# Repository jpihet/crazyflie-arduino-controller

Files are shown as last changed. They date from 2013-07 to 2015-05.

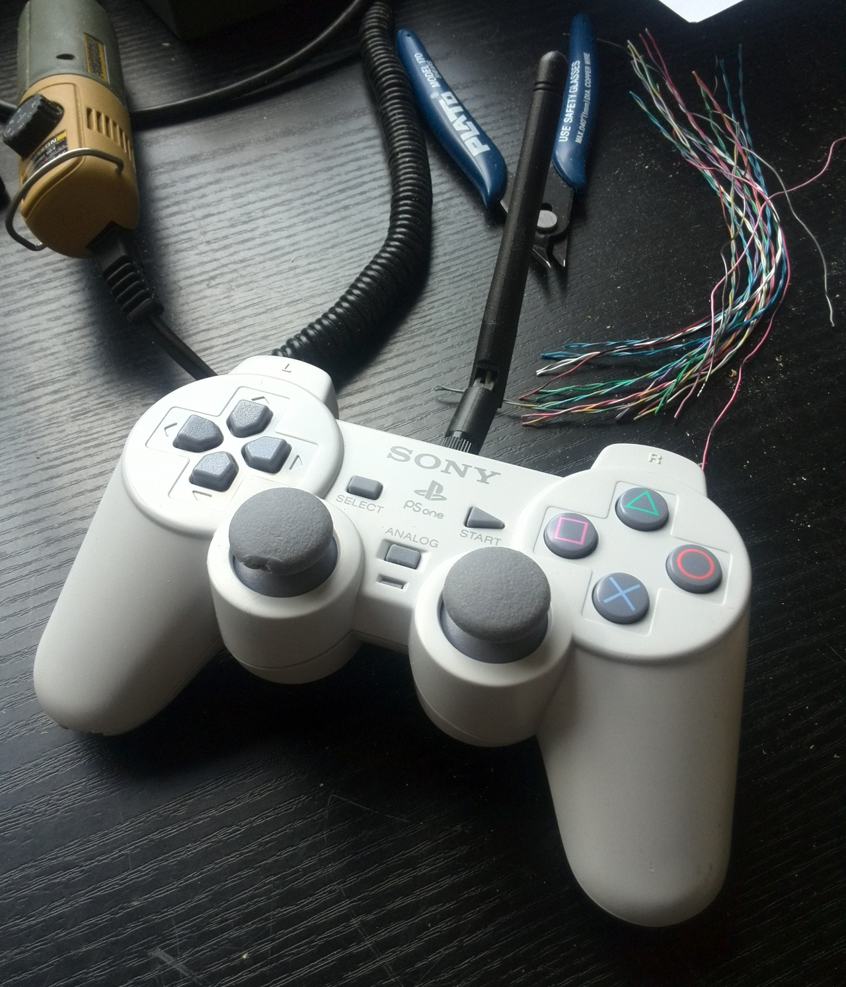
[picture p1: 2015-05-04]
Build_info/Crazyflie-Arduino-PS1_2.jpg

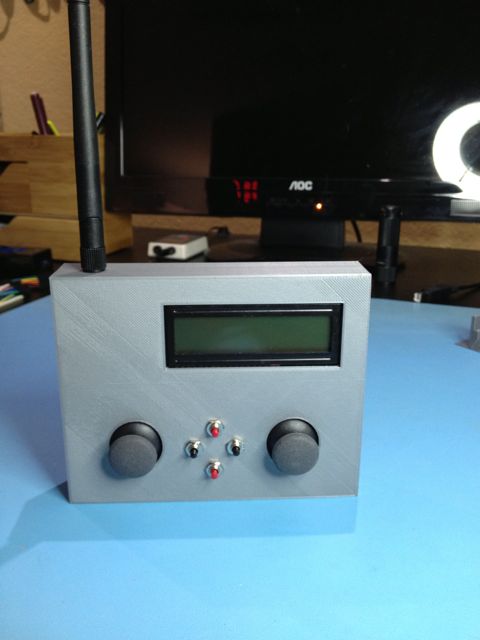
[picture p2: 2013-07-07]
Build_info/Case Front.jpg

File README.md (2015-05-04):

Crazyflie Arduino Controller Demo

This is a simple Arduino sketch to demonstrate the capability to use an Arduino
Nano connected to a h(ij)acked PS1 controller and a nRF24L01+PA board to fly a
CrazyFlie 2.0.

From tbitson's original project and code.

Wiring:
See code listing

Photos: see Build Info

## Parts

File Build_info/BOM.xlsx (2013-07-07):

Name | Source | PN | ID | Qty | Cost Ea | Comment
nRF24L001+ Breakout Board | Sparkfun | WRL-00705 |  | 1 | 19.95
Joystick, Thumb | Sparkfun | COM-09032 | JS1, JS2 | 2 | 3.95
Joystick Breakout Board | Sparkfun | BOB-09110 |  | 2 | 1.95
Arduino Pro Mini 5v 16MHz | Sparkfun | DEV-11113 | Arduino | 1 | 9.95
Serial LCD | Adafruit | 782 | LCD | 1 | 24.95
Antenna, 2.4 GHz Dipole | Adafruit | 944 | ANT1 | 1 | 6.95
Antenna, 2.4 GHz Dipole 5dBi Gain | Adafruit | 945 |  |  | 8.95 | Longer Range Option
Male Headers, strip | Adafruit | 392 |  | 100 | 7.95 | 10 Strips of 36
Jumpers, Female to Female | Sparkfun | PRT-08430 |  | 3 | 3.95 | pack of 10
Battery, Li Ion | Adafruit | 258 | B1 | 1 | 22.95 | Alternate - Use 3 AA
Charger/Booster, LiPo | Sparkfun | PRT-11231 |  | 1 | 19.95 | Convert battery to 5V
Switch, SPST | various | S7 |  | 1
Switch, pushbutton N.O. | various |  |  | 4
Proto-board for Power Bus | Adafruit | 589 |  | 1 | 8.95 | Pack of 3, only need 1
Case, 3-D Printed

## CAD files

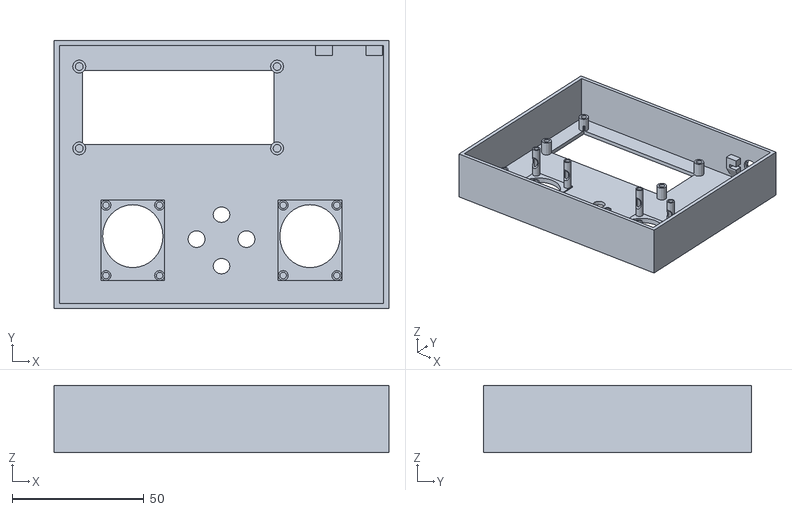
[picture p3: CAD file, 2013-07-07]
Build_info/crazyflie_controller_case.stl
127.0 x 101.6 x 25.4

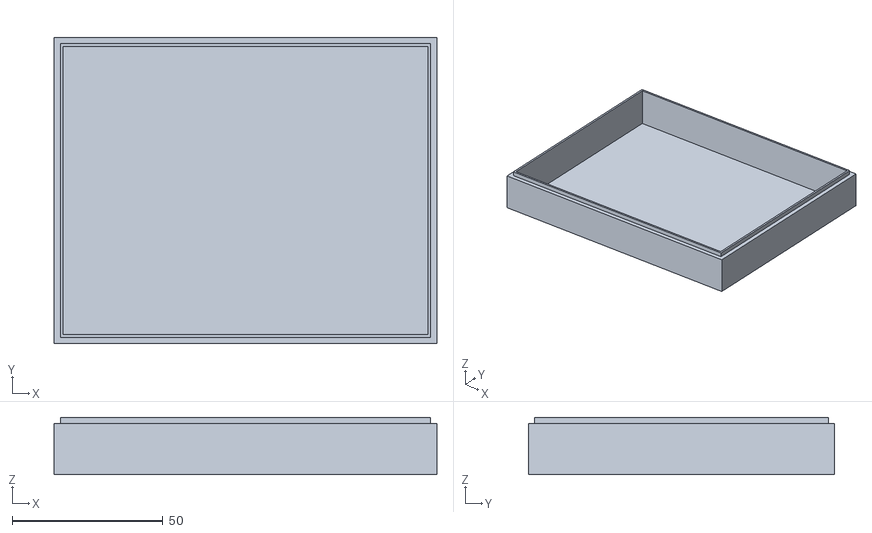
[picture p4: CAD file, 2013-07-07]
Build_info/crazyflie_controller_case_back.stl
127.0 x 101.6 x 19.1

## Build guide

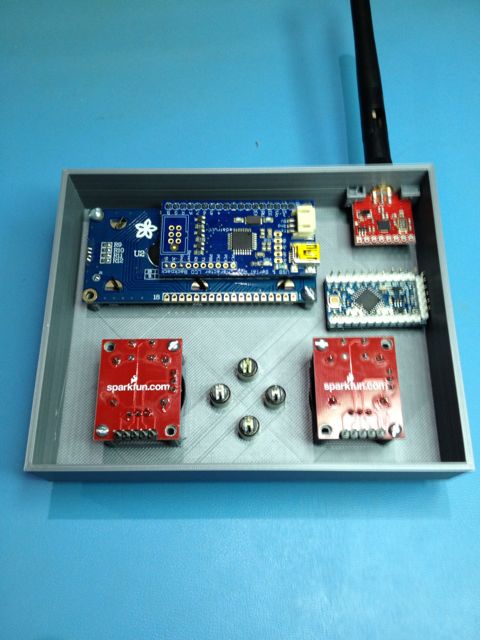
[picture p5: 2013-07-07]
Build_info/Inside - prior to wiring.jpg

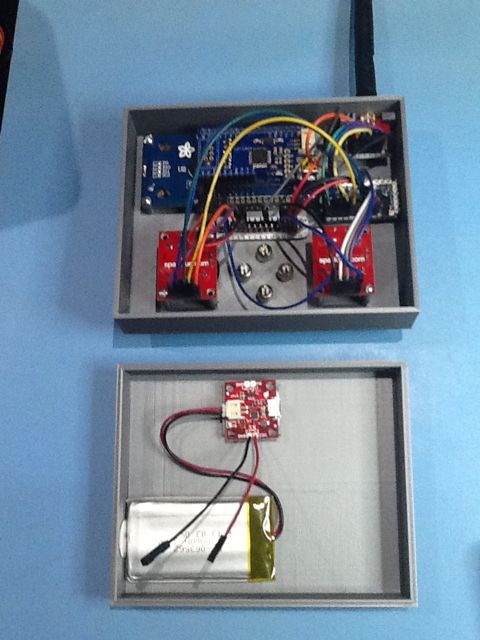
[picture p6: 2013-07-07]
Build_info/Inside - after wiring.jpg

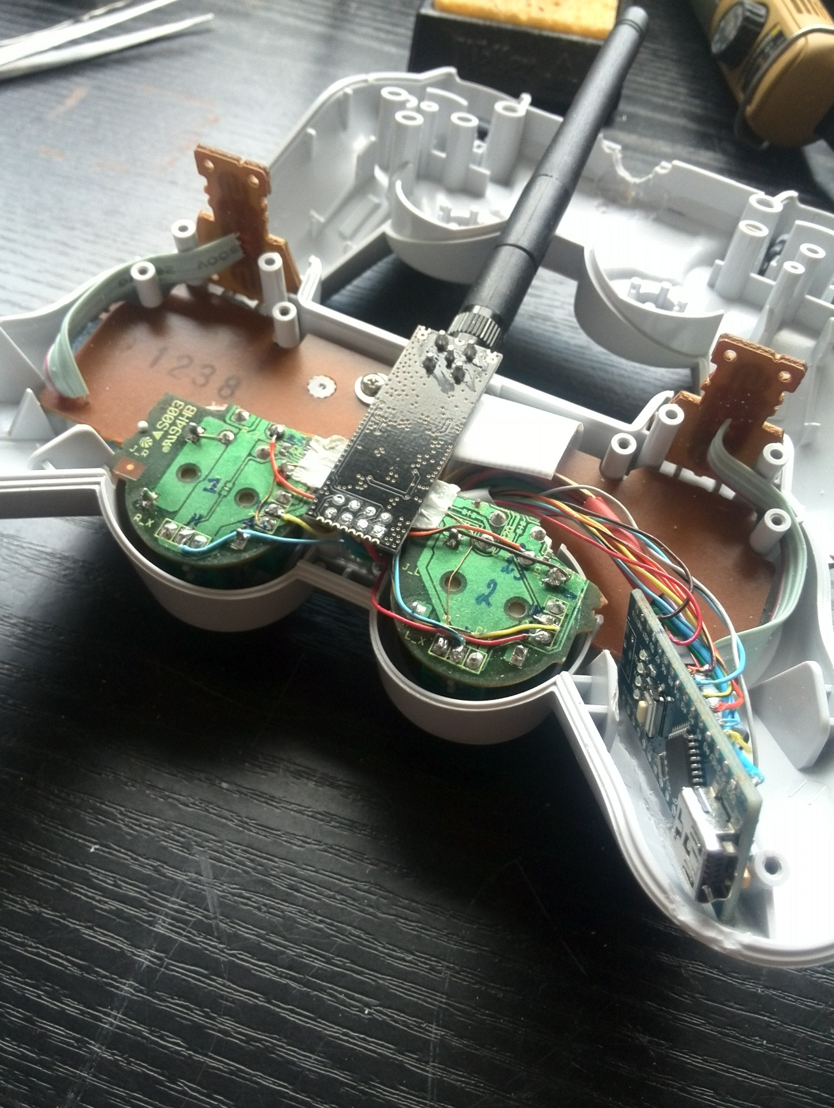
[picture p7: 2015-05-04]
Build_info/Crazyflie-Arduino-PS1_1.jpg

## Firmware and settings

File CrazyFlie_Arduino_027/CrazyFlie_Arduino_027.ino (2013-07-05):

/*   CrazyFlie Controller
 *   version 0.27  7/04/13 tbitson
 *
 * This program demonstarts controlling a CrazyFlie Quadcopter
 * using an Arduino. Based on the RF24 library by maniacbug at
 * https://github.com/maniacbug
 *
 * this is a very early prototype just to show its possible
 *
 *     TODO: 
 *     Get ACK packet to work
 *     Use 4 pushbuttons to adjust trim
 *     Add Logging & display remote battery capacity on LCD
 *     Fix thrust smoothing
 *     Convert LCD routines to a Arduinbo Libray
 *     Eliminate the RF24 library with direct nRF24L01 comm
 */


#include <SPI.h>
#include "nRF24L01.h"
#include "RF24.h"
#include "printf.h"
#include <SoftwareSerial.h>


// my defines
#define ulong uint32_t
#define uint  uint16_t

// enable debug prints by setting to 1
const boolean DEBUG = 0;

// connections
#define JS1_V   A0    // Thrust
#define JS1_H   A1    // Yaw
#define JS1_S   A2    // TBD

#define JS2_V   A3    // Pitch
#define JS2_H   A4    // Yaw
#define JS2_S   A5    // TBD

#define LCD_RX  2    // Rx
#define LCD_TX  3    // not connected

#define RF24_MOSI  11
#define RF24_MISO  12
#define RF24_SCK   13
#define RF24_IRQ   8   // not connected
#define RF24_CE    9
#define RF24_CSN   10

#define SW1    4    // switches unused in this version
#define SW2    5
#define SW3    6
#define SW4    7

#define LED  8

// from crazyflie firmware commander.c 
#define MIN_THRUST  10000
#define MAX_THRUST  50000
#define MIN_PITCH -30.0
#define MAX_PITCH  30.0
#define MIN_ROLL  -30.0
#define MAX_ROLL   30.0
#define MIN_YAW   -200.0
#define MAX_YAW    200.0

// hard coded offset values TODO: use switches to adjust
const int JS1_V_OFFSET = 497;    // thrust
const int JS1_H_OFFSET = 508;    // yaw
const int JS2_V_OFFSET = 510;    // pitch
const int JS2_H_OFFSET = 514;    // roll

// program defines
#define LOOP_TIME    100  // 100ms = 10 updates per second
#define SLEEP_MODE   0
#define PWR_ON_MODE  1

// joystick full scale value. Range 0 +/- 512 counts
const float JS_RANGE = 512.0;

// user set trim values TODO: store in EEPROM
int pitchOffset = 0;
int rollOffset = 0;
int yawOffset = 0;

// experimental thrust smoothing levels
const float ALPHA_UP = .50;
const float ALPHA_DOWN = .80;
float smoothedThrust = 0.0;


// Init RF24 lib. Pass CE and CSN pins
RF24 radio(RF24_CE, RF24_CSN);

// init LCD Serial port. Pass Rx and Tx pins
SoftwareSerial lcd(2, 3);


// define the packet we want to send
typedef struct
{
  byte addr;
  float roll;
  float pitch;
  float yaw;
  uint  thrust;
} 
cmdPacket;

// create an instance of the packet
cmdPacket crtp; 

// TODO: create a union with cmpPacket and byte array 

// send & receive array. Lame way to send struct
char payload[15];

// define a struct to store current state of I/O
typedef struct
{
  int thrust;
  int pitch;
  int yaw;
  int roll;
  boolean sw1;
  boolean sw2;
}  
controls;

//make an instance of the controls struct
controls cntr;


// program vars
ulong lastLoopTime = 0;
byte  mode = PWR_ON_MODE;





void setup(void)
{
  // let everything powerup & init
  delay(2000);

  Serial.begin(57600);
  Serial.println("CrazyFlie Arduino Controller ver 0.25");
  printf_begin();

  lcd.begin(57600);
  initSerialLCD();
  setLCDColor(0xFF, 0xFF, 0xFF);  // white
  lcd.print("CrazyFlie v0.25");

  // set up pin modes
  pinMode(LED, OUTPUT);
  pinMode(JS1_S, INPUT);
  pinMode(JS2_S, INPUT);

  // enable internal pullups on joystick switches
  digitalWrite(JS1_S, HIGH);
  digitalWrite(JS2_S, HIGH);

  // TODO: read control offsets if JS button is pushed
  // and store in EEPROM


  // define initial values for packet
  crtp.addr   = 0x30;
  crtp.roll   = 0.0;
  crtp.pitch  = 0.0;
  crtp.yaw    = 0.0;
  crtp.thrust = 0;

  // Setup and configure rf radio
  radio.begin();

  // enable dynamic payloads, ch 10, data rate 250K
  radio.enableDynamicPayloads();
  radio.setChannel(10);
  radio.setDataRate(RF24_250KBPS);
  radio.setRetries(5,3);
  radio.setCRCLength(RF24_CRC_16);
  radio.openWritingPipe(0xE7E7E7E7E7LL);
  radio.openReadingPipe(1, 0xE7E7E7E7E7LL);
  delay(100);

  // Dump the configuration of the rf unit for debugging
  if (DEBUG) radio.printDetails();

  // Start listening
  radio.startListening();

  Serial.println("setup done");
  //clearLCD();
}




void loop(void)
{
  // loop if desired time has passed
  if ((millis() - lastLoopTime) > LOOP_TIME)
  {
    lastLoopTime = millis();

    // read controls
    readControls();

    // check if we should enter/exit low power mode
    checkPowerStatus();

    // if low power mode, just exit
    if (mode == SLEEP_MODE) return;

    // scale controls to expected CF values
    processControls();

    if (DEBUG) printCntrValues();
    if (DEBUG) printCRTPValues();

    // send data to Cazyflie
    sendData();

    // check various stuff
    checkStatus();

    // show current status and info on LCD
    updateLCD();
  }
}





void readControls()
{
  // read pitch and roll on joystick 1
  cntr.thrust = analogRead(JS1_V);
  cntr.yaw    = analogRead(JS1_H);
  cntr.sw1    = !digitalRead(JS1_S);

  // read throttle & yaw on joystick 2
  cntr.pitch = analogRead(JS2_V);
  cntr.roll  = analogRead(JS2_H);
  cntr.sw2   = !digitalRead(JS2_S);

  // TODO: add debouce to switches if pressed
}


void processControls()
{
  // thrust is 10000 to 50000
  // pitch is -30.00 to +30.00
  // roll is -3000 to +30.00
  // yaw is -199.99 to +199.99

  float alpha;

  // first subtract offsets from joystick
  cntr.thrust -= JS1_V_OFFSET;
  cntr.yaw -= JS1_H_OFFSET;
  cntr.pitch -= JS2_V_OFFSET;
  cntr.roll -= JS2_H_OFFSET;

  // scale to crazyflie values
  float thrust = ((float)cntr.thrust - 10.0) * MAX_THRUST/512.0;
  crtp.pitch = (float)cntr.pitch * MAX_PITCH/512.0 * -1.0;
  crtp.roll =  (float)cntr.roll * MAX_ROLL/512.0 * -1.0;
  crtp.yaw =   (float)cntr.yaw * MAX_YAW/512.0;

  // experimental filter to smooth thrust power
  if (thrust < 0) thrust = 0;
  if (thrust < smoothedThrust)
    alpha = ALPHA_DOWN;
  else
    alpha = ALPHA_UP;

  // running average filter
  smoothedThrust = alpha * smoothedThrust + (1.0 - alpha) * thrust;
  crtp.thrust = (uint)smoothedThrust;

  if (DEBUG)
  {
    Serial.print("thrust = ");
    Serial.print(thrust);
    Serial.print("   smoothed thrust = ");
    Serial.println(smoothedThrust);
  }

  // check if in bounds
  if (crtp.thrust < MIN_THRUST) crtp.thrust = 0;
  if (crtp.thrust > MAX_THRUST) crtp.thrust = MAX_THRUST;

  constrain(crtp.pitch, MIN_PITCH, MAX_PITCH);
  constrain(crtp.roll, MIN_ROLL, MAX_ROLL);
  constrain(crtp.yaw, MIN_YAW, MAX_YAW);
}




void checkStatus(void)
{
  // TODO: check battery voltage
  // TODO: check link status
}


void updateLCD()
{
  setLCDCursor(1, 2);

  lcd.print("T:");
  lcd.print(cntr.thrust);
  lcd.print(" P:");
  lcd.print(cntr.pitch);

  lcd.print(" R:");
  lcd.print(cntr.roll);
  lcd.print(" ");

}





void sendData(void)
{
  // turn on LED to show we're sending
  digitalWrite(LED, HIGH);

  // First, stop listening so we can talk.
  radio.stopListening();

  // copy the struct into a byte array
  memcpy(&payload, &crtp, sizeof(crtp));

  // send the packet. Blocks until sent
  if (DEBUG) Serial.println("Sending...");
  radio.write(payload, sizeof(crtp) );

  // turn off LED
  digitalWrite(LED, LOW);

  // start listening for an ACK
  radio.startListening();

  // Wait here until we get a response, or timeout
  ulong start = millis();
  boolean timeout = false;
  while ( !radio.available() && !timeout )
  {
    if (millis() - start > 10)
      timeout = true;
  }

  // Did we timeout?
  if (timeout)
  {
    if (DEBUG) Serial.println("response timed out");
  }
  else
  {
    // read response
    uint8_t len = radio.getDynamicPayloadSize();
    radio.read(payload, len );

    // display response
    Serial.print("Got response: size= ");
    Serial.println(len);
  }

  // delay for debugging
  //delay(1000);
}



void printCntrValues()
{
  Serial.print("Thrust = ");
  Serial.print(cntr.thrust);
  Serial.print("  Yaw = ");
  Serial.print(cntr.yaw);
  Serial.print("  Pitch = ");
  Serial.print(cntr.pitch);
  Serial.print("  Roll = ");
  Serial.print(cntr.roll);
  Serial.print("  SW1 = ");
  Serial.print(cntr.sw1);
  Serial.print("  SW2 = ");
  Serial.println(cntr.sw2);
}


void printCRTPValues()
{
  Serial.print("ADDR = ");
  Serial.print(crtp.addr, HEX);
  Serial.print("  Roll = ");
  Serial.print(crtp.roll);
  Serial.print("  Pitch = ");
  Serial.print(crtp.pitch);
  Serial.print("  Yaw = ");
  Serial.print(crtp.yaw);
  Serial.print("  Thrust = ");
  Serial.println(crtp.thrust);
}


void checkPowerStatus()
{
  // check if both joystick switches are on
  if (cntr.sw1 && cntr.sw2)
  {
    // wait 2 seconds and check again
    delay(2000);
    readControls();

    // if the buttons are still down, switch modes
    if (cntr.sw1 && cntr.sw2)
    { 
      if (mode == PWR_ON_MODE)
      {
        // power down
        setLCDDisplayOn(0);
        mode = SLEEP_MODE;
        // TODO: Put nRF24L01 & arduino to low power mode
      }
      else
      {
        // power up
        setLCDDisplayOn(1);
        mode = PWR_ON_MODE;
      }
    }
  }
}



// LCD Routines - TODO: convert this to a lib ----------

void initSerialLCD()
{
  setLCDSize(16, 2);
  setLCDContrast(200);      
  setLCDBrightness(255);     
  setLCDDisplayOn(1);

  // turn off cursors
  lcd.write(0xFE);
  lcd.write(0x4B);
  
  // block curson off
  lcd.write(0xFE);
  lcd.write(0x54);

  // turn off autoscroll
  lcd.write(0xFE);
  lcd.write(0x52);

  clearLCD();
}


void clearLCD()
{
  // clear screen
  lcd.write(0xFE);
  lcd.write(0x58);
  delay(1);
}


void setLCDSize(byte cols, byte rows)
{
  lcd.write(0xFE);
  lcd.write(0xD1);
  lcd.write(cols);  // default = 16 columns
  lcd.write(rows);  // default = 2 rows
  delay(10);
}


void setLCDDisplayOn(byte val)
{
  lcd.write(0xFE);

  if (val > 0)
  {
    lcd.write(0x42);
    lcd.write(0xFF);
  }
  else
    lcd.write(0x46);

}


void setLCDBrightness(byte val)
{
  lcd.write(0xFE);
  lcd.write(0x99);
  lcd.write(val);
}

void setLCDContrast(byte val)
{
  lcd.write(0xFE);
  lcd.write(0x50);
  lcd.write(val);
}

void setLCDBaud(byte val)
{
  // 0x10 = 57600
  // 0x22 = 28800
  // 0x33 = 19200
  // 0x67 = 9600 (default)
  
  lcd.write(0xFE);
  lcd.write(0x39);
  lcd.write(val);
  delay(10);
}


void homeLCD()
{
  // go 'home'
  lcd.write(0xFE);
  lcd.write(0x48);
  delay(1);  
}

void setLCDCursor(byte col, byte row)
{
  // set curson to col & row position
  lcd.write(0xFE);
  lcd.write(0x47);
  lcd.write(col);
  lcd.write(row);
}


void setLCDColor(byte r, byte g, byte b)
{
  lcd.write(0xFE);
  lcd.write(0xD0);
  lcd.write(r); 
  lcd.write(g);
  lcd.write(b);
  delay(1);
}

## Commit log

2013-07-07 Updated README Bill of Materials
2013-07-07 Additional support files added
    [BOM.xlsx, crazyflie_controller_case.stl, crazyflie_controller_case_back.stl]
2013-07-07 Tweaks to throttle filter
2013-07-07 Tweaked throttle smoothing filter values. Updated README to include bill of materials. Changes directory and file name to be compatible with git
2015-04-29 Remove printf
    Using Serial debugging output
2015-05-04 Calibrate joysticks at every startup and on demand
    On demand = when both joysticks buttons are pressed for 2sec.
2015-05-04 Debug: add HEX dump of radio data
    + minor fixes
    [CrazyFlie_Arduino.ino]
2015-05-04 Joystick: PS1 controller specifics
    Calibrated joystick ranges, polarity etc.
2015-05-04 Crazyflie 2.0 - Arduino Nano - PS1 Controller
    Updated README
    Added pics of the build
